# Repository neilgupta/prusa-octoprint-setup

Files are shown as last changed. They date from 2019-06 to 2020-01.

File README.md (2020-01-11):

# OctoPrint setup for Prusa MK3S

Prusa recommends using a Raspberry Pi Zero W to run [OctoPrint](http://octoprint.org/) for your printer. While this is very clean and easy, it is underpowered and you can't get a camera. You also risk the print failing if you are checking its status too often via the UI or app. Here's my setup for attaching a Raspberry Pi 3B+, camera, and lights to a Prusa MK3S printer for a reliable OctoPrint server with a camera. The total cost is about $100.

## Hardware

* Raspberry Pi 3B+
* 16GB microSD Card
* Raspberry Pi Camera v2
* 1 meter ribbon cable for camera
* WS2812 LED light strip

## Prints

### Raspberry Pi Mount - Bottom

https://www.thingiverse.com/thing:2843889

Resolution: 0.15

Infill: 20% (optional)

### Raspberry Pi Mount - Lid

http://www.thingiverse.com/thing:559858

Resolution: 0.1

Infill: 20%

### Camera Mount - Arm, Camera, Lid, Post

https://www.prusaprinters.org/prints/7064-customizable-raspberry-pi-camera-bed-mount-prusa-m/

Customizable via included OpenSCAD, but the gcode files committed here should work great with an MK3S. This mount does require using a couple of the spare M4 screws included with your Prusa.

Material: PLA should be safe, but PETG is better given its proximity to heat bed

Resolution: 0.2

Infill: 20%

### Ribbon clips

http://www.thingiverse.com/thing:3189351

**Print 4 of these!**

Resolution: 0.2

Infill: 10%

## Octoprint

1. Flash Raspberry Pi SD card with [OctoPi](https://github.com/guysoft/OctoPi) image
2. Set wifi password in `octopi-wpa-supplicant.txt`
3. Boot up raspberry pi and `ssh pi@octopi.local`
4. `passwd` to change root password
5. Edit `/etc/hostname` to give this octopi a unique name
6. Visit `http://octopi.local` in browser
6. Configure [Prusa MK3S printer profile](https://github.com/prusa3d/OctoPi/blob/devel/src/modules/octopi/filesystem/home/pi/.octoprint/printerProfiles/_default.profile)
7. Install octoslack and octopod plugins
8. Restart Raspberry Pi
9. Configure plugins as needed
10. Happy printing!

## Lighting

This repo also includes a script that can control a WS2812 LED light strip attached to the raspberry pi. It will dynamically change lights based on the status of the printer. I use [these ones](https://www.amazon.com/gp/product/B00JYPJAL2/) but Adafruit's NeoPixels will work well too.

1. Connect lights to raspberry pi

Trim led strip to 15 pixels so that they fit on the top frame of the MK3S. Solder 3 wires (65cm length each) to connect led strip to 5V, GND, and GPIO pin 18. I also use a [Texas Instruments SN74AHCT125N buffer](https://www.digikey.com/product-detail/en/texas-instruments/SN74AHCT125N/296-4655-5-ND/375798) to ensure correct logic voltage, but this is optional. My Raspberry Pi 3B+ was able to drive the LED strip with 3.3v logic.

Mount the led strip to the bottom of the frame with double sided tape and use 4 zip ties to hold in place, since the heat from the lights + extruder will weaken the tape very quickly.

2. Clone this repo

```bash
git clone https://github.com/neilgupta/prusa-octoprint-setup.git
cd prusa-octoprint-setup
```

3. Install dependencies

```bash
sudo apt-get update
sudo apt-get install -y python3-pip
sudo pip3 install -r requirements.txt
```

4. Install [MQTT plugin](https://github.com/OctoPrint/OctoPrint-MQTT) in Octoprint, configure it to talk to `hiome.local`. This assumes you have [Hiome](https://hiome.com)... if not, get on that first! Set the topic format to `_hiome/1/sensor/CLIENT_NAME/` where `CLIENT_NAME` is "prusa_" + octopi's hostname (ie "prusa_octopi")

5. Install led systemd service

```bash
sudo cp octoprint-led.service /etc/systemd/system/octoprint-led.service
sudo systemctl enable octoprint-led.service
sudo systemctl start octoprint-led.service
```

To run the script as a one-off, it's `sudo python3 led.py`

6. Start a print from octoprint!

<div align="center">
  <a href="https://raw.githubusercontent.com/neilgupta/prusa-octoprint-setup/master/prusa.jpeg">
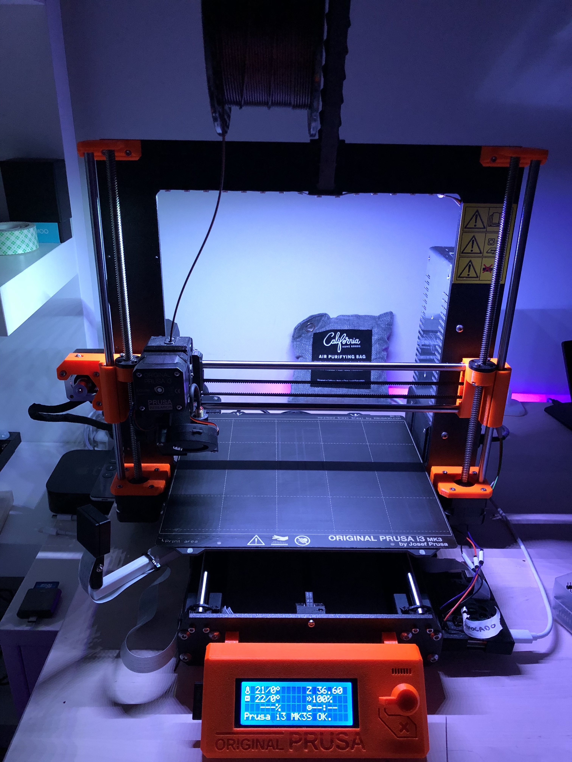
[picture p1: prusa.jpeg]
My Prusa MK3S
    
  </a>
</div>

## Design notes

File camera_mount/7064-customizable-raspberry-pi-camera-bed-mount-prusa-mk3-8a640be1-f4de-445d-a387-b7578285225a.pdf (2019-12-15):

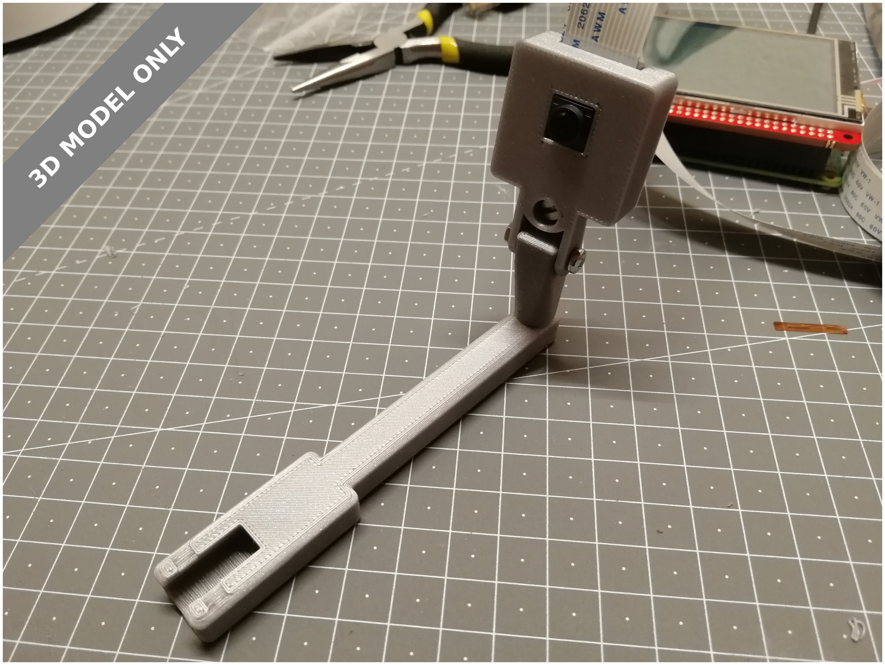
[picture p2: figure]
3D MODEL ONLY

## Summary

Currently for Prusa MK3 and the Raspberry Pi Camera only, but other printers could easily be added.

This was heavily inspired by jgeyer's Prusa i3 MK2/MK3 Raspberry Camera Mount (https://www.thingiverse.com/thing:2736439) and it's remixes. However everything was redesigned in OpenSCAD to make it much easier to customize in the future.
Parts

This thing contains multiple parts to print:

- the camera housing to fit the Raspberry Pi Camera v2 (should also work with v1)
- the lid to close the housing
- the post the camera is mounted on
- the arm where the post is attached to and which is mounted on the bed frame Everything is assembled with M3 screws. The arm simply slides over the bed frame and can optionally be fixated with a zip tie. The fit should be good enough to not need the zip tie though.
Customizing

The design can be customized. you can decide

- if the lid should be screwed on

Andreas Gohr (https://www.prusaprinters.org/social/965/prints)

## Customizable Raspberry Pi Camera Bed Mount (Prusa MK3)

VIEW IN BROWSER (https://www.prusaprinters.org/prints/7064-customizable-raspberry-pi-camera-bed-mount-prusa-m)

updated 18. 10. 2019 | published 18. 10. 2019

Model Files (.stl, .3mf, .obj, .amf) | DOWNLOAD ALL FILES (https://www.prusaprinters.org/prints/7064-customizable-raspberry-pi-camera-bed-mount-prusa-m/files)

484.6 KB
updated 18. 10. 2019 | (https://www.prusaprinters.org/prints/7064-customizable-raspberry-pi-camera-bed-mount-prusa-m/files)

1.6 MB
updated 18. 10. 2019 | (https://www.prusaprinters.org/prints/7064-customizable-raspberry-pi-camera-bed-mount-prusa-m/files)
- if the cable should come out at the top or bottom
- how long the arm should be
- at what angle the arm should be mounted (fits right and left side)
- how tall the post should be Click "Open in Customizer" to customize.
Printing

I recommend a brim for printing the post. The arm is printed with the opening towards the bed, the slight slack of the bridging helps with the tight fit. If your printer can't do these bridges, feel free to flip the part.

Please post a make if you make one.
Sources

The sources are available at Github. (https://github.com/splitbrain/openscad-projects/tree/master/bedcamera) If you want to extend or reuse parts of this, please use the sources (multiple .scad files) at Github instead of the single file version at Thingiverse.

Pull-Requests to add more printers, cameras or other attachments welcome!

3D Printers (https://www.prusaprinters.org/prints?categoryId=1) > 3D Printers - Upgrades (https://www.prusaprinters.org/prints?categoryId=2)

raspberrypicamera | prusai3mk3 | prusai3 | originalprusai3mk3
customizer | customizable | cameramount

Printer Brand: Prusa Printer: i3 MK3 (http://amzn.to/2rqZ6Uo) Rafts: No Supports: No Resolution: 0.2mm Infill: 20% Filament: Prusa PLA silver

lid.stl

arm.stl

501.4 KB
updated 18. 10. 2019 | (https://www.prusaprinters.org/prints/7064-customizable-raspberry-pi-camera-bed-mount-prusa-m/files)

3.2 MB
updated 18. 10. 2019 | (https://www.prusaprinters.org/prints/7064-customizable-raspberry-pi-camera-bed-mount-prusa-m/files)

14.2 KB
updated 18. 10. 2019 | (https://www.prusaprinters.org/prints/7064-customizable-raspberry-pi-camera-bed-mount-prusa-m/files)

649.1 KB
updated 18. 10. 2019 | (https://www.prusaprinters.org/prints/7064-customizable-raspberry-pi-camera-bed-mount-prusa-m/files)

Find source .stl files on Thingiverse.com (https://www.thingiverse.com/thing:3182262)

The Author has not uploaded any G-codes.
Try to search in User G-codes (https://www.prusaprinters.org/prints/7064-customizable-raspberry-pi-camera-bed-mount-prusa-m/user-gcodes) section or generate and upload your own.

## License

This work is licensed under a
Creative Commons (4.0 International License)

Attribution (http://creativecommons.org/licenses/by/4.0/)

✖ | Sharing without ATTRIBUTION
✔ | Remix Culture allowed
✔ | Commercial Use
✔ | Free Cultural Works
✔ | Meets Open Definition

camera.stl

all.stl

combined.scad

post.stl

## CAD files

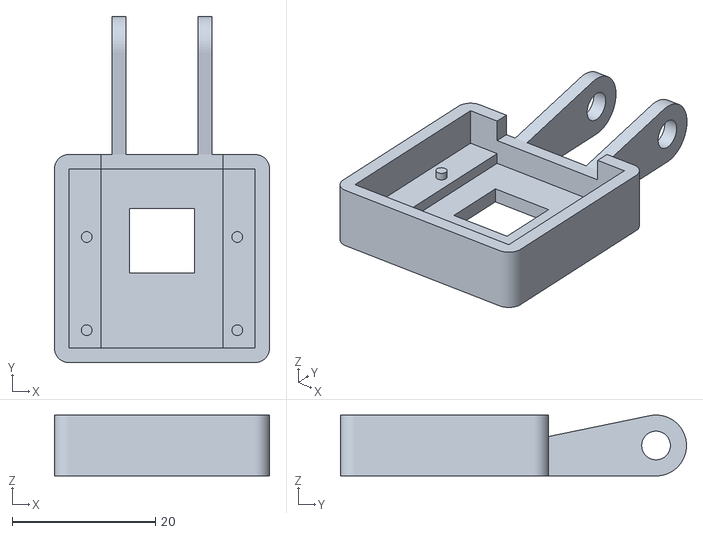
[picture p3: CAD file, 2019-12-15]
camera_mount/camera.stl
30.0 x 48.2 x 8.50

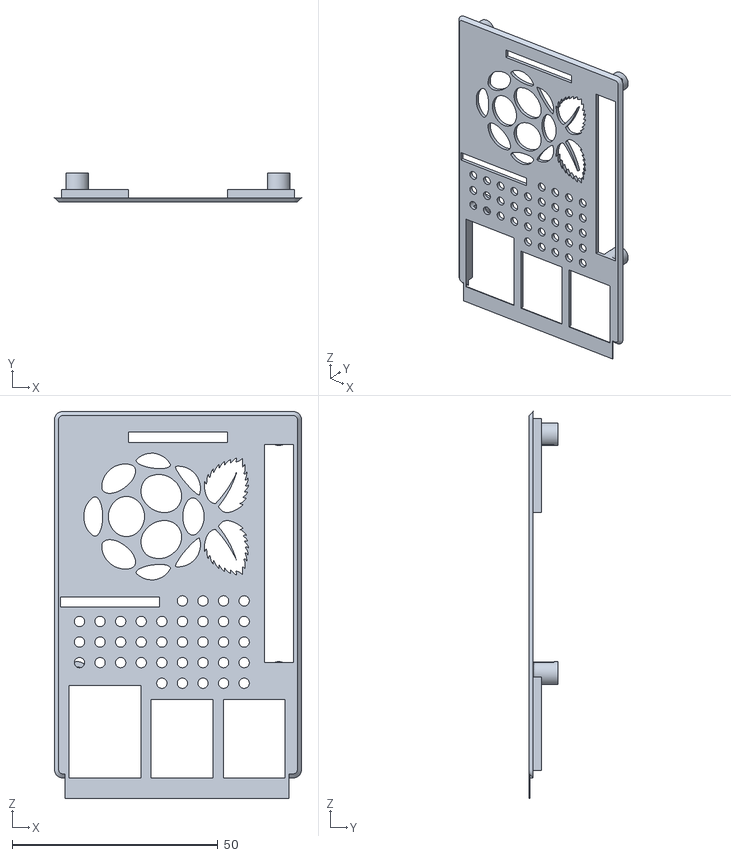
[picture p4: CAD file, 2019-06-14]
pi_mount/lid.stl
60.0 x 7.00 x 94.0

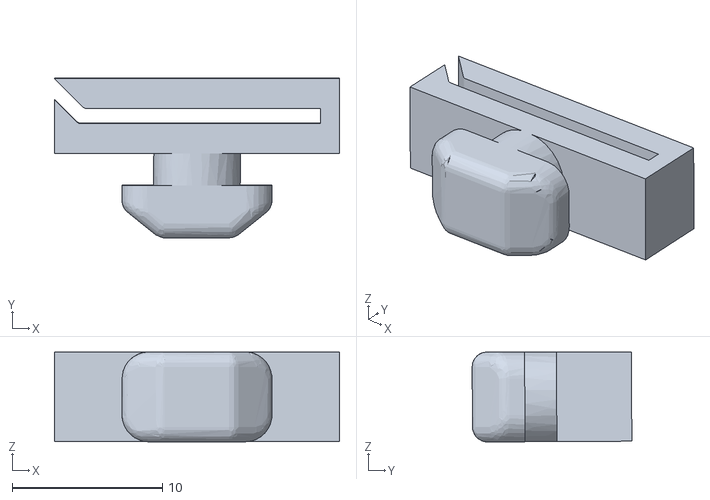
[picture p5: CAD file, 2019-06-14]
ribbon_cable_clip_v2_6mm.stl
19.0 x 10.6 x 6.00

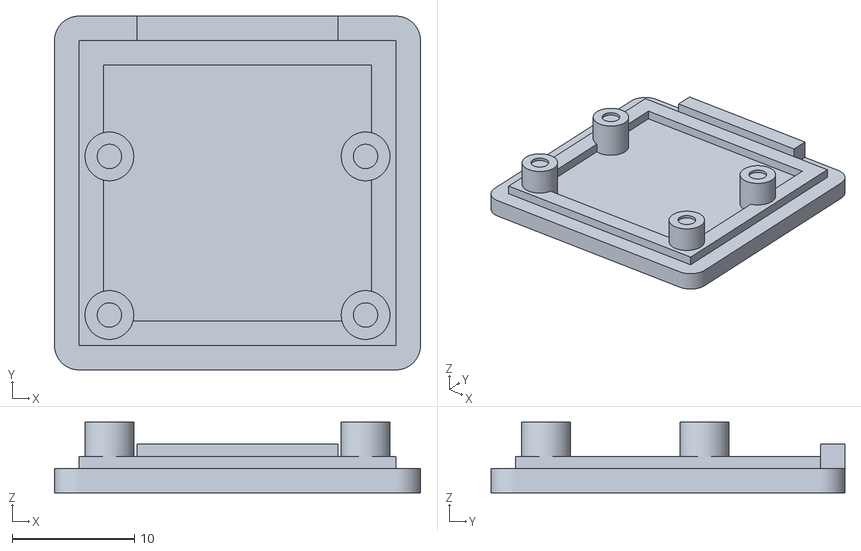
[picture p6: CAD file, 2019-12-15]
camera_mount/lid.stl
30.0 x 29.0 x 5.80

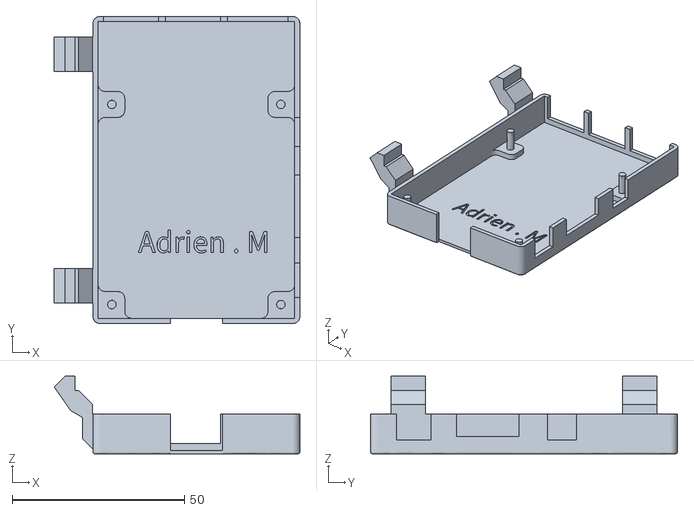
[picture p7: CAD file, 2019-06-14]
pi_mount/bottom.stl
71.2 x 89.0 x 22.5

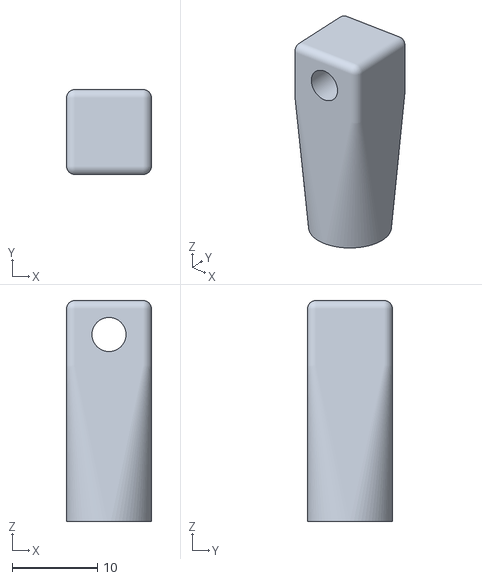
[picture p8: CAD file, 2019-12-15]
camera_mount/post.stl
10.0 x 10.00 x 26.0

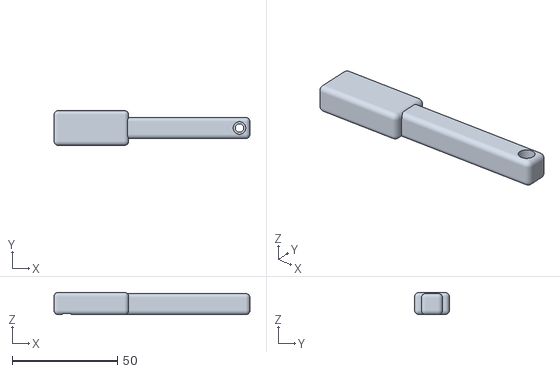
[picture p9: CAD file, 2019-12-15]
camera_mount/arm.stl
93.1 x 16.5 x 10.5

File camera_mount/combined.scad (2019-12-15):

/* START main.scad*/
/* START customizer.scad*/
/* [General] */

// Which part do you want to access?
cnf_part = "arm"; // [camera:Camera Body, lid:Camera Lid, post:Camera Post, arm:Bed Mounting Arm, all:All]

/* [Camera Case] */

// Do want to screw the lid on the camera body?
cnf_lidscrew = 0; // [0: no, 1: yes]

// Do you want to flip the camera and have the cable at the bottom?
cnf_flip = 1; // [0: no, 1: yes]

/* [Bed Mounting Arm] */

// Which type of arm do you need? Currently only one available
cnf_armtype = "mk3"; // [mk3:Prusa MK3]

// Length of the arm from the mount (mm)
cnf_armlength = 70;

// Rotation of the arm (deg)
cnf_armrotation = 0; // [-45:45]

/* [Camera Post] */

// height of the camera post (mm)
cnf_postheight = 26;

/* [Advanced] */

// smothness of rounded edges
$fn = 70;

// Thickness of Walls (mm)
cnf_walls = 2;

// size of screw holes (mm)
cnf_screw = 4;

// size of screw heads (for sinking them) (mm)
cnf_screwhead = 6;

// size of tap holes (mm)
cnf_drill = 3;

/* [Hidden] */
/* END customizer.scad*/
/* START picamera.scad*/
/* START primitives.scad*/
/**
 * A centered cube, but flat on the Z-Surface
 */
module ccube(v) {
    translate([0, 0, v.z/2]) cube(v, true);
}

/**
 * An upright standing centered cylinder, flat on the Z-Surface
 */
module ccylinder_y(h, d) {
    translate([h/-2, 0, d/2])
        rotate([0, 90, 0])
            cylinder(h=h, d=d);
}

/**
 * Creates a rounded cube
 *
 * @param {vector} v The size of the cube
 * @param {number} r The radius of the rounding
 * @param {bool} flatcenter centered but flat on Z
 */
module roundedCube(v, r=1, flatcenter=true) {
    mv = flatcenter ? [0,0,0] : [v.x/2, v.y/2 ,0];

    translate(mv) hull() {
        // right back bottom
        translate([v.x/2 - r, v.y/2 - r, r])
            sphere(r=r);

        // right front bottom
        translate([v.x/2 - r, v.y/-2 + r, r])
            sphere(r=r);

        // left back bottom
        translate([v.x/-2 + r, v.y/2 - r, r])
            sphere(r=r);

        // left front bottom
        translate([v.x/-2 + r, v.y/-2 + r, r])
            sphere(r=r);


        // right back top
        translate([v.x/2 - r, v.y/2 - r, v.z - r])
            sphere(r=r);

        // right front top
        translate([v.x/2 - r, v.y/-2 + r, v.z - r])
            sphere(r=r);

        // left back top
        translate([v.x/-2 + r, v.y/2 - r, v.z - r])
            sphere(r=r);

        // left front top
        translate([v.x/-2 + r, v.y/-2 + r, v.z - r])
            sphere(r=r);
    }
}
/* END primitives.scad*/

//picamera(part="camera");
//picamera(part="lid");

/**
 * Creates the body or lid for the camera
 *
 * @param {string} part The part to print, either "camera" or "lid"
 * @param {bool} flip Should the cable come out of the bottom?
 * @param {bool} lidscrew Should the be screwed on?
 * @param {number} walls The wall thickness in mm
 * @param {number} screw The diameter of the screw hole
 * @param {number} screwhead The diameter of the screw head hole
 */
module picamera (
    part = "camera",
    flip = false,
    lidscrew = true,
    walls = 2,
    screw = 4,
    screwhead = 4
) {
    // basic setup
    pcb = [26, 25, 1];
    pcb_part = [17, pcb.y, 1.5];
    cable_z = 1; // above pcb
    pcb_clear = 4;
    tab = 14;
    body_z   = walls+pcb.z+pcb_part.z+pcb_clear;
    holder_z = walls+pcb.z+pcb_part.z+cable_z;
    $fn = $fn ? $fn : 90;

    // print part
    if(part == "camera") {
        camera();
    } else {
        lid();
    }

    /**
     * The lid
     */
    module lid() {
        ridge=1; // thickness of the inner ridge
        cable=1; // space for the cable
        pin_off=0.2;

        // the lid itself
        linear_extrude(height=walls) {
            offset(r=walls) {
                square([pcb.x, pcb.y],true);
            }
        }

        translate([0,0,walls]) {
            // the inner ridge
            difference() {
                linear_extrude(height=ridge) {
                    square([pcb.x, pcb.y],true);
                }

                linear_extrude(height=ridge) {
                    offset(r=walls*-1) {
                        square([pcb.x, pcb.y],true);
                    }
                }
            }
            // the pins holding the pcb down (half a rigde shorter)
            difference(){
                pins(4, pcb_clear-pin_off);
                translate([0,0,pcb_clear-ridge/2]) pins(2, ridge);
            }

            // closes the cable outlet (half a ridge smaller than the outlet)
            translate([0, (pcb.y+walls) /2,0]) {
                ccube([pcb_part.x-ridge/2, walls, pcb_clear-cable_z-cable]);
            }
        }

        // the tab for screwing down the lid
        if(lidscrew) translate([0, -1*pcb.y/2, 0]) {
            tab();
        }
    }

    /**
     * Create the camera case
     */
    module camera() {
        holder_space = 10;
        mod = flip ? 1 : -1;

        body();

        // add two arms
        translate([0, mod*(pcb.y/2 + walls), 0]) {
            translate([(holder_space+walls)/-2, 0 , 0]) {
                holderarm(flip);
            }
            translate([(holder_space+walls)/2, 0 , 0]) {
                holderarm(flip);
            }
        }

        // mechanism to screw the lid on
        if(lidscrew) translate([0, pcb.y/-2, 0]) {
            closer();
        }
    }

    /**
     * Screw mechanism for the lid
     *
     * Basically the same as the closer() but we don't need to cut
     * the cylinder and we have no sink hole for the screw head
     */
    module tab() {
        translate([0,-1*walls,0]) {
            difference() {
                cylinder(h=walls, d=tab);
                translate([0, screwhead/-2, walls/-2]) {
                    cylinder(h=walls*2, d=screw);
                }
            }
        }
    }

    /**
     * Screw mechanism for the case
     *
     * Basically the same as the tab() but with a sunken hole for the
     * screw head.
     */
    module closer() {
        translate([0,-1*walls,0]) {
            difference() {
                cylinder(h=body_z, d=tab);

                // drill holes for head and screw
                translate([0, screwhead/-2, 0]) {
                    cylinder(h=body_z/2, d=screwhead);
                    cylinder(h=body_z*2, d=screw);
                }

                // cut off a little less than half
                translate([0, tab/2 + walls, body_z/-2]) {
                    ccube([tab, tab, body_z*2]);
                };
            }
        }
    }

    /**
     * Creates a single holder arm
     */
    module holderarm() {
        length = 10;

        rot = flip ? 180 : 0;

        rotate([0,0,rot]) {
            translate([0,length/-2,0]) {
                difference() {
                    // tapered shape for when the cable is at the same end
                    hull() {
                        ccube([walls, length, holder_z]);
                        translate([0, -1*length, 0]) {
                            ccylinder_y(walls, body_z);
                        }
                    }

                    // the screw hole
                    translate([0, -1*length, body_z/2-screw/2]) {
                        ccylinder_y(walls*2, screw);
                    }
                }
            }
        }
    }

    /**
     * Creates the camera body
     */
    module body() {
        difference() {
            linear_extrude(height=body_z) {
                offset(r=walls) {
                    square([pcb.x, pcb.y],true);
                }
            }
            pcb_cutout();
        }
    }

    /**
     * the 4 pins to hold the pcb
     */
    module pins(d, h) {
        pin_off_w = 2.5; // center from walls
        pin_off_y = 13; // distance upper from lower pin center

        // lower right
        translate([(pcb.x/-2)+pin_off_w, (pcb.y/-2)+pin_off_w, 0]) {
            cylinder(h=h, d=d);
        }

        // lower left
        translate([(pcb.x/2)-pin_off_w, (pcb.y/-2)+pin_off_w, 0]) {
            cylinder(h=h, d=d);
        }

        // upper right
        translate([(pcb.x/-2)+pin_off_w, (pcb.y/-2)+pin_off_w+pin_off_y, 0]) {
            cylinder(h=h, d=d);
        }

        // upper left
        translate([(pcb.x/2)-pin_off_w, (pcb.y/-2)+pin_off_w+pin_off_y, 0]) {
            cylinder(h=h, d=d);
        }
    }

    /**
     * Carves the space for the PCB
     */
    module pcb_cutout() {
        lens = [9, 9, walls];
        lens_yoffset = 2.5; // from center
        pin_d = 1.5;
        cut = lens.z + pcb_part.z + pcb.z; // cut through all

        difference() {
            union() {
                translate([0, lens_yoffset, -1]) {
                    ccube([lens.x, lens.y, lens.z+1], true); // lens
                }
                translate([0,0,lens.z]) {
                    ccube([pcb_part.x, pcb_part.y, pcb_part.z], true); // front parts
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

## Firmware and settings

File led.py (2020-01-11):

#!/usr/bin/python3

import board
import neopixel
import random
import time
import socket
import paho.mqtt.client as mqtt

hostname = socket.gethostname()
CLIENT_NAME = 'prusa_'+hostname
MQTT_HOST = 'hiome.local'
MQTT_PORT = 1883

topic = '_hiome/1/sensor/' + CLIENT_NAME + '/event/'

pixels = neopixel.NeoPixel(board.D18, 15)

OFF   = (0,0,0)
WHITE = (255,255,255)
RED   = (255,0,0)
YELLOW= (255,255,0)
GREEN = (0,128,0)

currentColor = OFF
def setLight(newColor):
  pixels.fill(newColor)
  currentColor = newColor

def onMessage(client, userdata, msg):
  if msg.topic == topic + 'PrintStarted':
    setLight(WHITE)
  elif msg.topic == topic + 'PrintDone':
    setLight(OFF)
  elif msg.topic == topic + 'PrintCancelling':
    setLight(YELLOW)
  elif msg.topic == topic + 'PrintCancelled':
    setLight(OFF)
  elif msg.topic == topic + 'PrintPaused':
    setLight(YELLOW)
  elif msg.topic == topic + 'PrintResumed':
    setLight(WHITE)
  elif msg.topic == topic + 'PrintFailed':
    setLight(RED)
  elif msg.topic == topic + 'Error':
    setLight(RED)
  elif msg.topic == topic + 'Upload':
    # flash green for 10 seconds
    oldColor = currentColor
    setLight(GREEN)
    time.sleep(5)
    setLight(oldColor)
    time.sleep(1)
    setLight(GREEN)
    time.sleep(4)
    setLight(oldColor)
  elif msg.topic == topic + 'Connecting':
    setLight(GREEN)
  elif msg.topic == topic + 'Connected':
    setLight(OFF)
  elif msg.topic == topic + 'Disconnecting':
    setLight(YELLOW)
  elif msg.topic == topic + 'Disconnected':
    setLight(OFF)
  elif msg.topic == '_hiome/1/sensor/' + CLIENT_NAME + '/status' and msg.payload == 'disconnected':
    setLight(RED)

def onConnect(client, userdata, flags, rc):
  client.subscribe('_hiome/1/sensor/' + CLIENT_NAME + '/#', qos=1)
  setLight(OFF)

client = mqtt.Client(client_id=CLIENT_NAME, clean_session=False)
client.on_connect = onConnect
client.on_message = onMessage
client.connect(MQTT_HOST, MQTT_PORT, 60)
client.loop_forever()

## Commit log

2019-12-15 replace crappy camera mount with better one
    [MK2PressFitLid.stl, MK3cameramount.stl, Prusa_MK3_Bed_Camera_Mount_1.0-BodyInverted.stl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]
2019-12-15 rename folders to be more sensible
    [arm.stl, bottom.stl, camera.stl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]
2019-12-22 add led service software
